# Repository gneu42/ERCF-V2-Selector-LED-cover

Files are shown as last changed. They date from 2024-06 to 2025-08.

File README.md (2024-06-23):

<h1 align="center">ERCF-Selector-LED-cover</h1> 
<H2 align="center">Under construction : use it with caution. </H2>
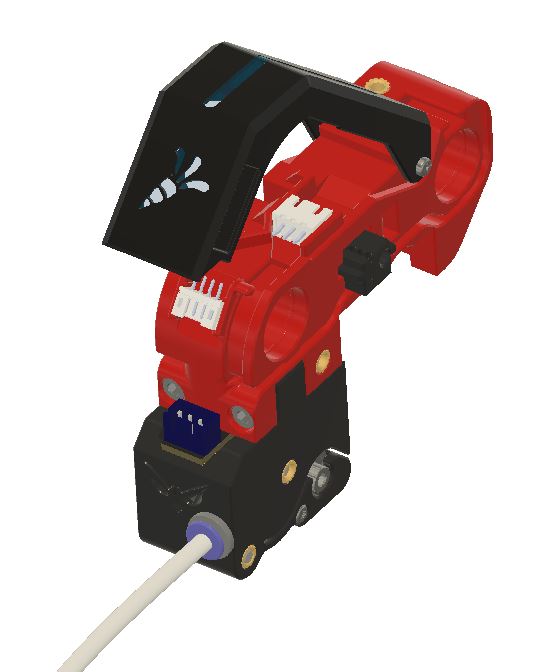
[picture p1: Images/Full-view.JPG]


**To be able to add LEDs in the selector cover, you need to print the new selector and encoder.**
* The new selector have a second cable channel on the right side to allow the LED wires to come to the front. The servo holder had its own screew now. A 4 pins PH connector power the status LED and the give the DATA to the 3 pins XH connector that feed the cover LED. 
* Why a new encoder ? Because at a certain point in time, I had a lot of problem with the encoder. I had remove it to clean it. To solve that problem I decide to move the screws to the front, and made some other improvments :
  * New adjustable berake
  * Removeble brearing cover
  * The bearing can be adjusted to be in line with the BMG
  * ECAS is hold in place tighter
  * Opening around the bearing so it can be cleaned easily.
  * The bottom secret screw is back
  * Status LED insert in the eyes. The Binky LED shows in the mouth
* The cover LED has 7 LEDs to display the filament movement, 1 LED for the leafs, and 1 LED for the carrot. 
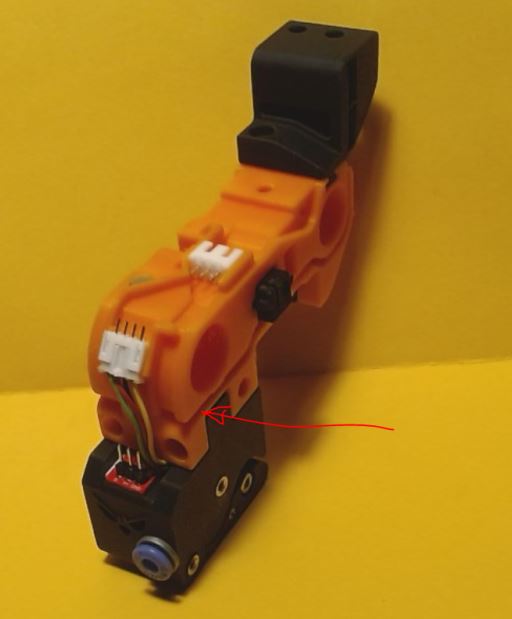
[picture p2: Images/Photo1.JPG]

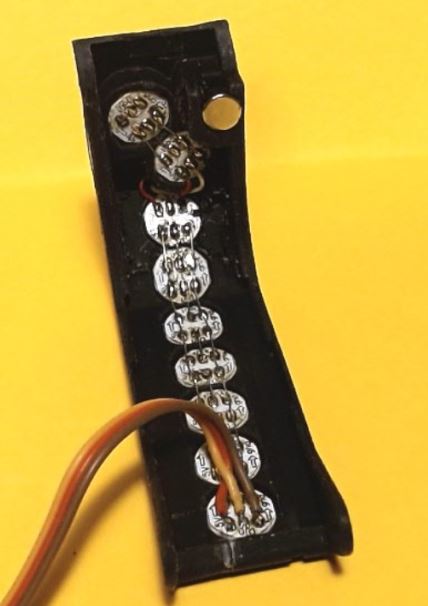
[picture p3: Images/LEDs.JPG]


The encoder and selector are tested. 
The new cover, is not yet tested.

## Summary.
* **[Bom](#bom)**
* **[Printing Tips](#printing-tips)**
* **[Assembling tips](#assembling-tips)**
 
# more to come shortly...

# BOM

# Printing tips
* The cover must be printed in 2 colors. The windows should be printed in transparent color. Load the cover in the slicer and split it into parts, then assign the colors to each bodies.

# Assembling tips

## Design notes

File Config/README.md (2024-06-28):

# **This explain how to set up the LOGO , Staus and Cover LEDs.**

##In your printer.cfg file, add :
```
   [include cover_leds_macros.cfg]
```

##In /config/mmu/base/mmu_macro_vars.cfg change the following variables 
````
[gcode_macro _MMU_STATE_VARS]
description: Happy Hare configuration for state change hooks
gcode: # Leave empty
 # You can extend functionality to all Happy Hare state change macros by
 # adding a command (or call to your gcode macro). E.g for additional
 # LED logic
 variable_user_action_changed_extension      : "_MMU_ACTION_CHANGED_COVER"    ; Executed after default logic with duplicate params
 variable_user_print_state_changed_extension : "_MMU_PRINT_STATE_CHANGED_COVER"    ; Executed after default logic with duplicate params
 variable_user_gate_map_changed_extension    : ""    ;Executed after default logic with duplicate params
 ````

**This is my personnal config as example, you must make the changes needed to match your setup :**

I have the barf led in the gearbox, 13 exit leds, no entry leds, 7 leds for the cover bar graph, 2 leds for the cover carrot logo.
    I have the following chain : 
  * From the RGB connector on the ERB board 
  * => Gearbox Barf (1-8) 
  * => Exit range (9-21) 
  * => status_index (22) 
  * => cover leds (23-29) 
  * => cover logo leafs (30) 
  * => cover logo carrot (31)

## In /config/mmu/base/mmu_hardware.cfg modify the neopixel mmu_leds according your setup.
```
[neopixel mmu_leds]
pin: mmu:MMU_NEOPIXEL
chain_count: 31              # Number gates x1 or x2 + 1 (if you want status)
color_order: GRB, GRB, GRB, GRB, GRB, GRB, GRB, GRB, GRBW, GRBW, GRBW, GRBW, GRBW, GRBW, GRBW, GRBW, GRBW, GRBW, GRBW, GRBW, GRBW, GRBW, GRBW, GRBW, GRBW, GRBW, GRBW, GRBW, GRBW, GRBW, GRBW        # Set based on your particular neopixel specification

[mmu_leds]
num_gates: 13
led_strip: neopixel:mmu_leds
exit_range: 9-21   
#entry_range: 14-{mmu_num_leds}
status_index: 22   
frame_rate: 24
```

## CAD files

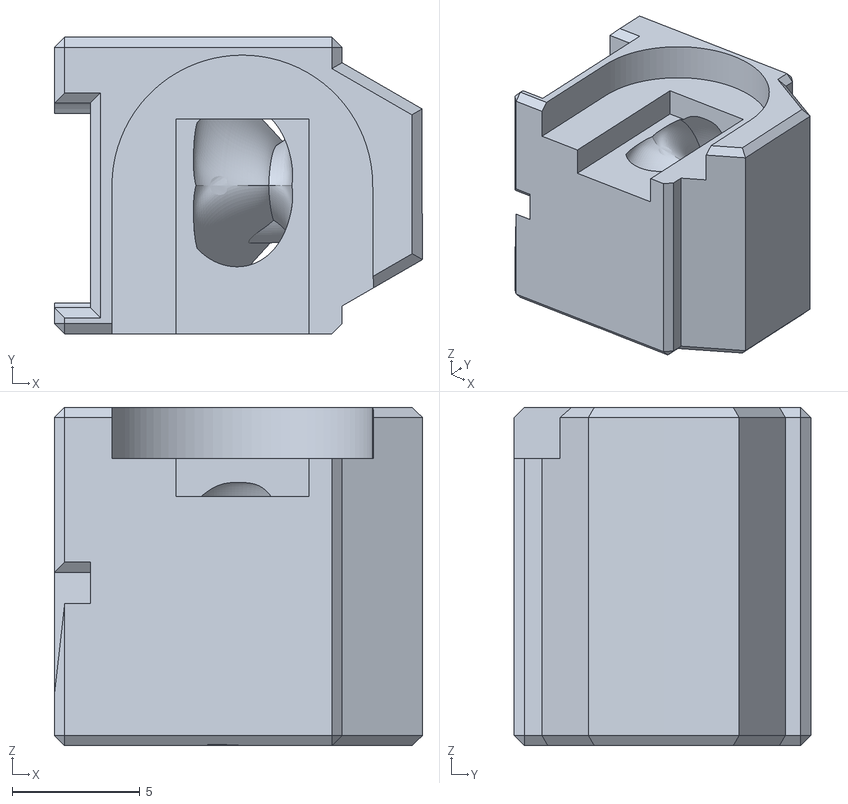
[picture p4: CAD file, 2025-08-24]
STL/[W]Encoder_Insert.stl
14.4 x 11.6 x 13.2

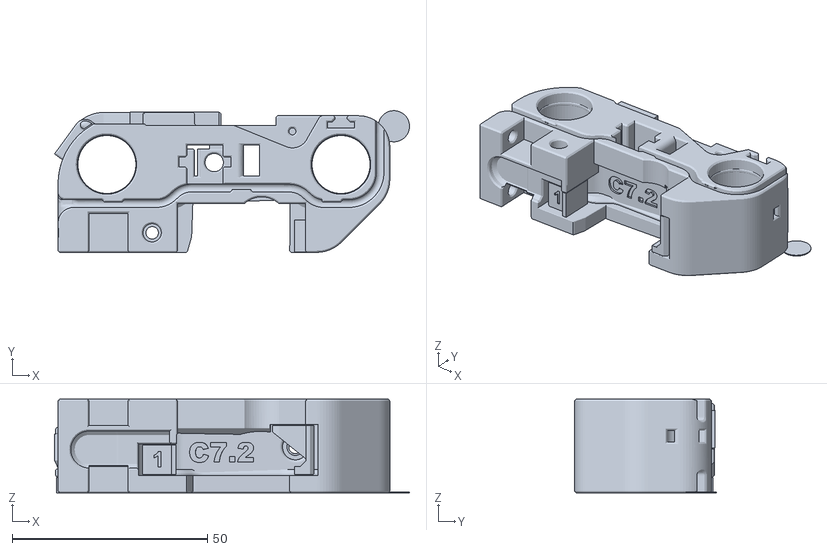
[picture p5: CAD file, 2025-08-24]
STL/[a]Selector_Cart_for_Cover_LED_Support_Corrected.stl
91.0 x 36.3 x 24.0

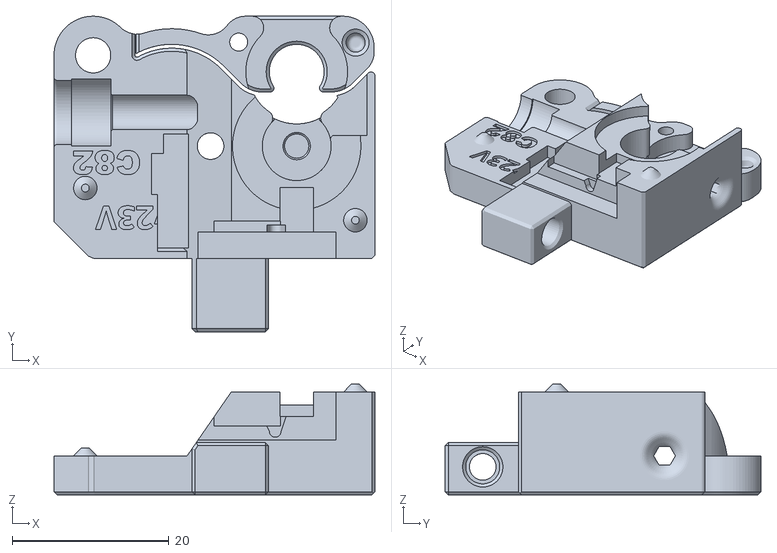
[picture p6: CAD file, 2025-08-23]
STL/Encoder_Right.stl
41.0 x 40.3 x 14.2

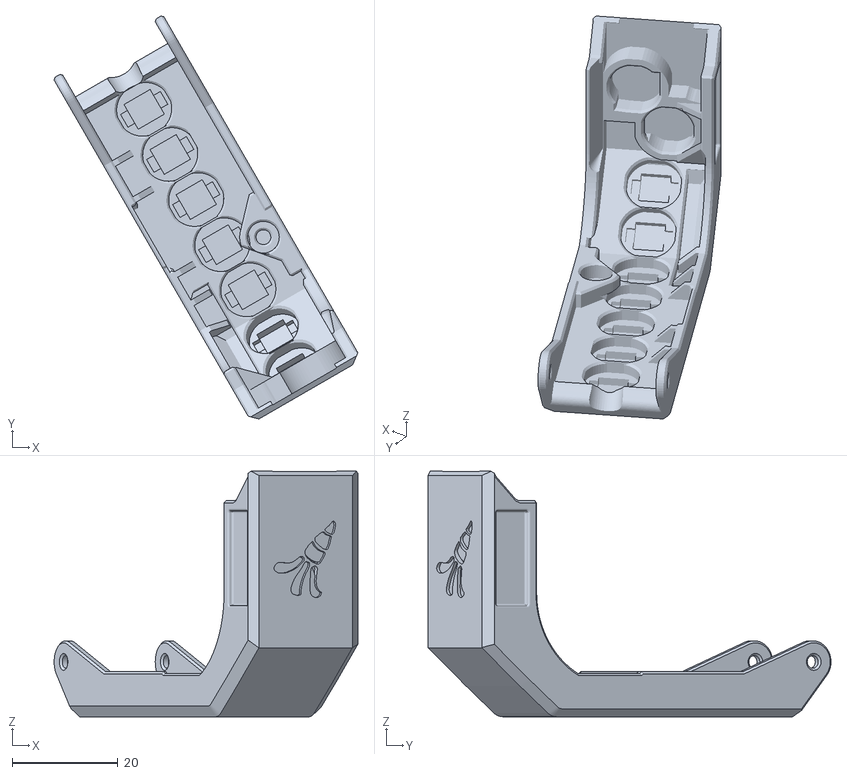
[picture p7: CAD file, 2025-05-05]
STL/Selector_Door_W_LED_Nosupports.stl
57.5 x 76.3 x 46.5

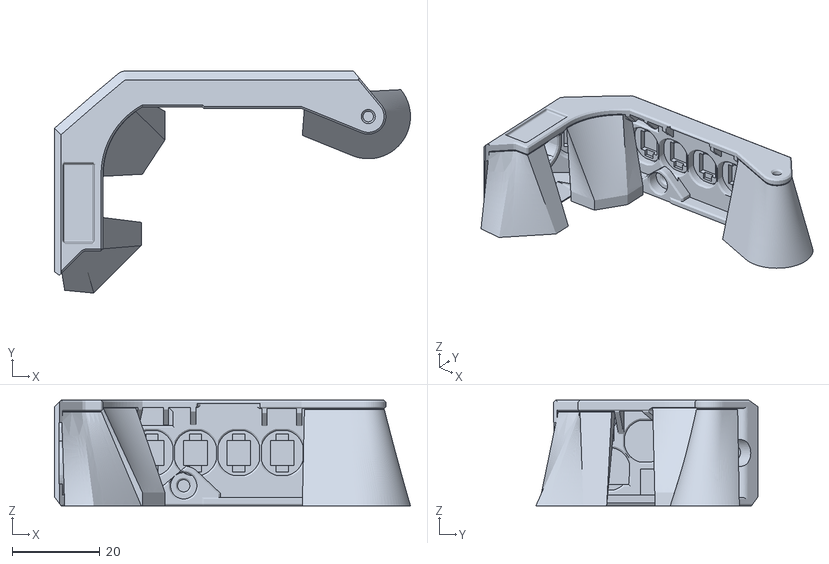
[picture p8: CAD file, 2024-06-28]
STL/Selector_Door_W_LED.stl
80.9 x 50.5 x 24.0

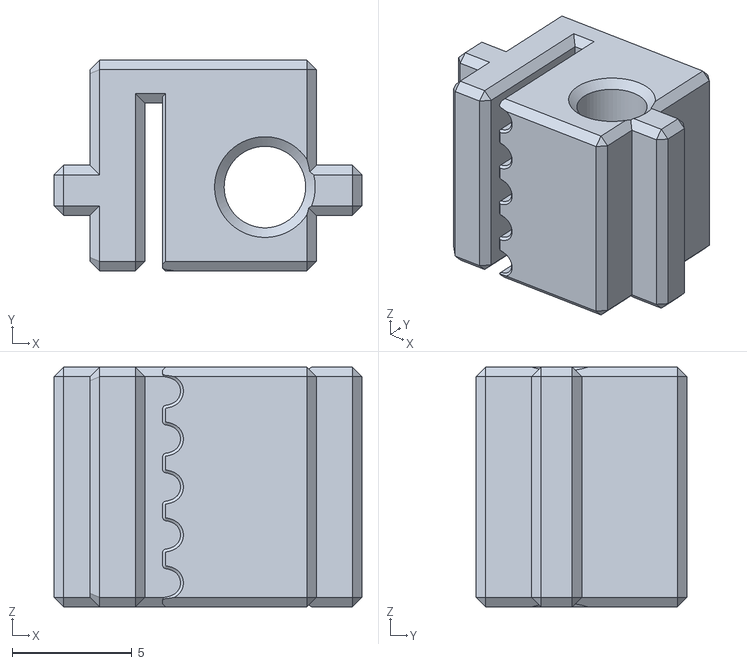
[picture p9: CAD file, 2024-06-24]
STL/Optional_Belt_Tensionner_thik.stl
12.8 x 8.80 x 10.0

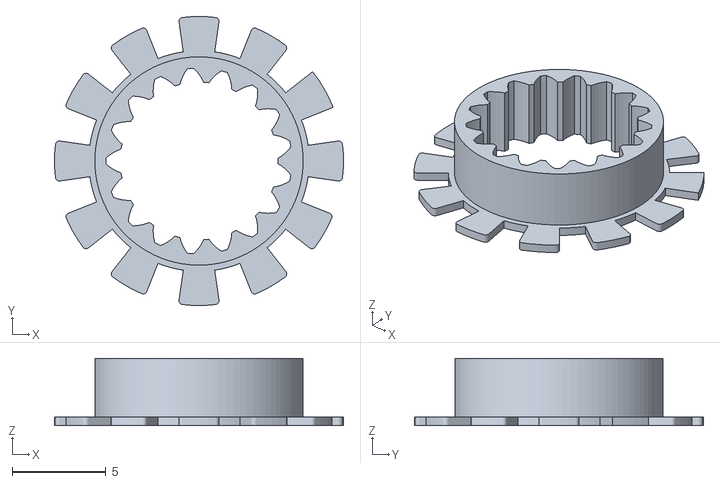
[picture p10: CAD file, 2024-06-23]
STL/[B]Optional_Slotted wheel_045mm.stl
15.4 x 15.4 x 3.58

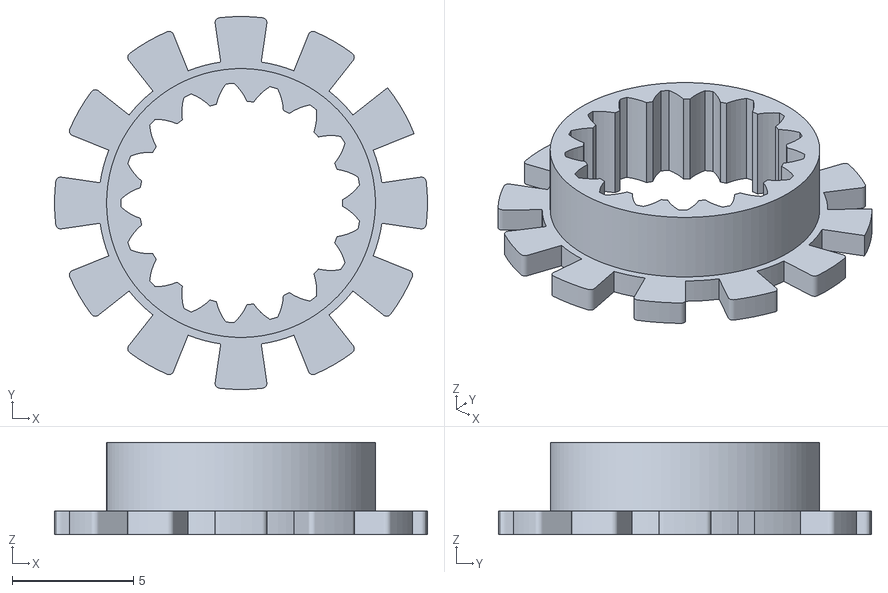
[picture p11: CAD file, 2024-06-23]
STL/[B]Original_Encoder_Slotted_Wheel.stl
15.4 x 15.4 x 3.80

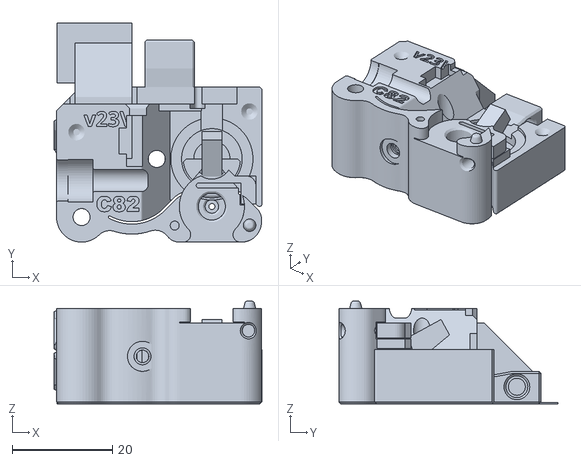
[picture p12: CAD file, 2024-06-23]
STL/Encoder_Left.stl
41.5 x 43.8 x 20.5

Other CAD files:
STL/[a]Selector_Cart_for_Cover_LED.stl

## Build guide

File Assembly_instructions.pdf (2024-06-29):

ERCF LED Cover.

Assembly manual.

This manual explain how to deal with the cover LED specific parts, please refer to the ERCF V2 manual for everything that is not in this manual.

Encoder.

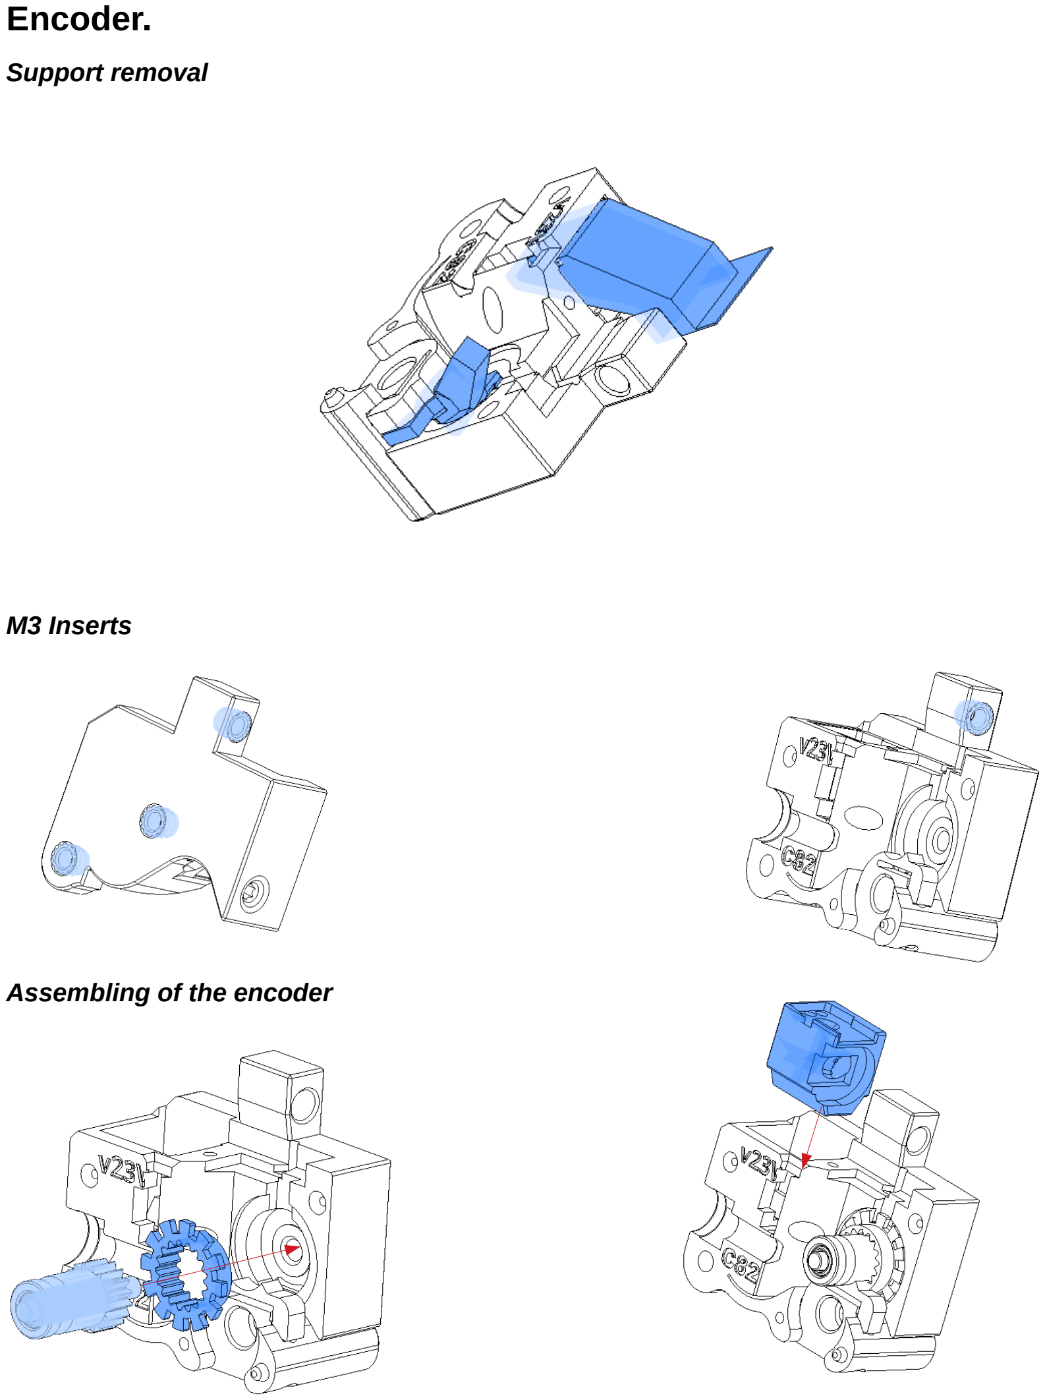
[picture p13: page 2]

Support removal

M3 Inserts

Assembling of the encoder

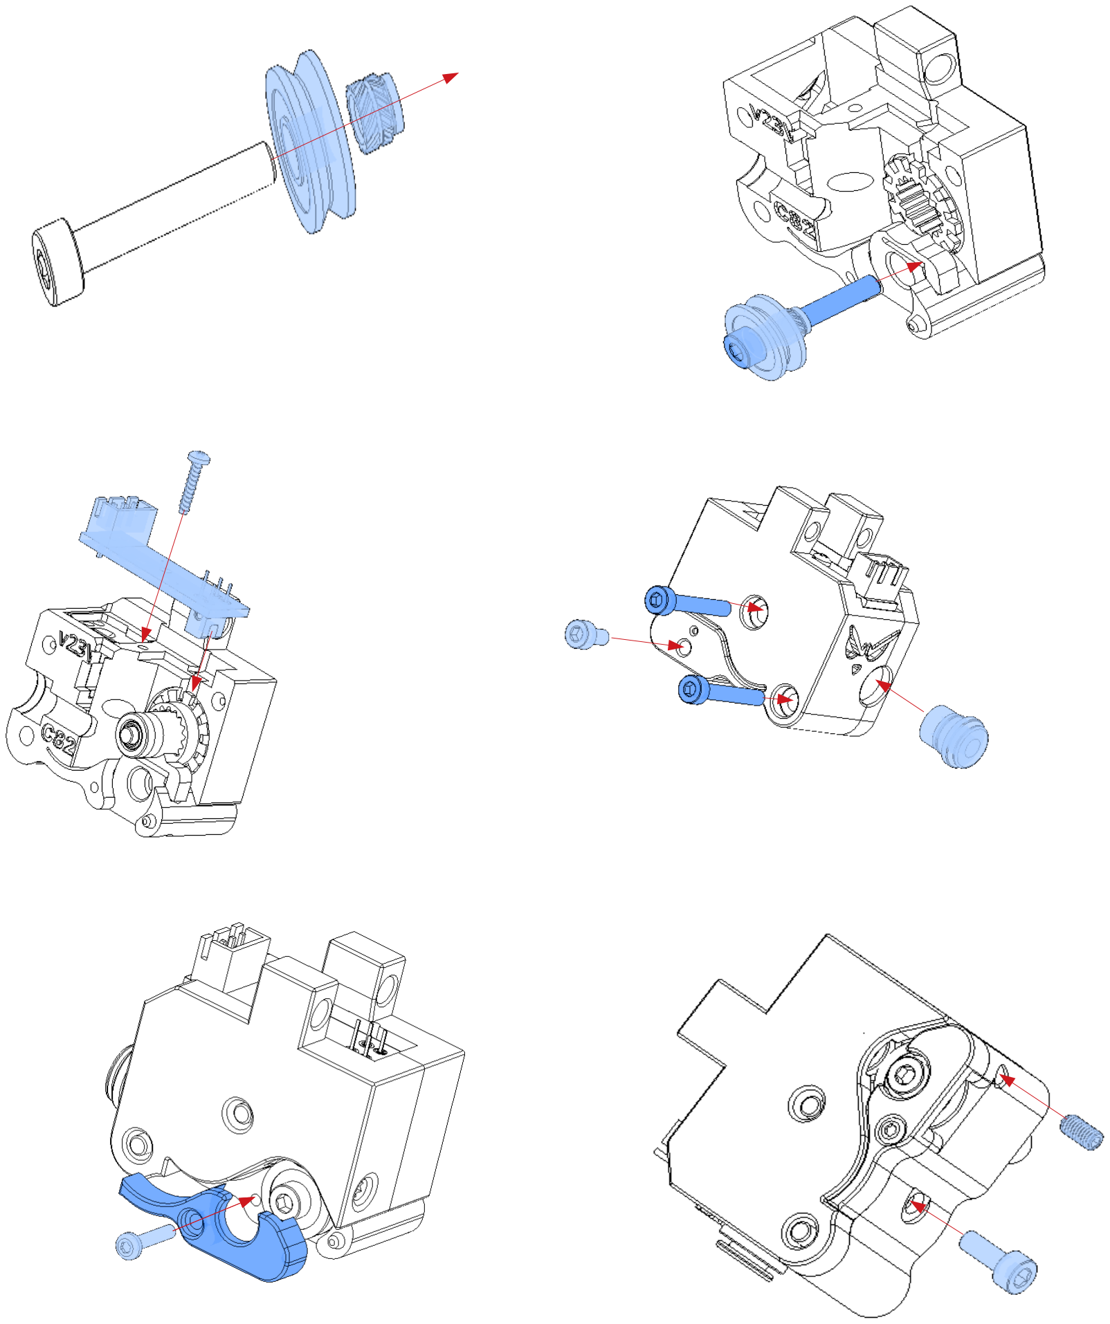
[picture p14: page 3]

## Selector

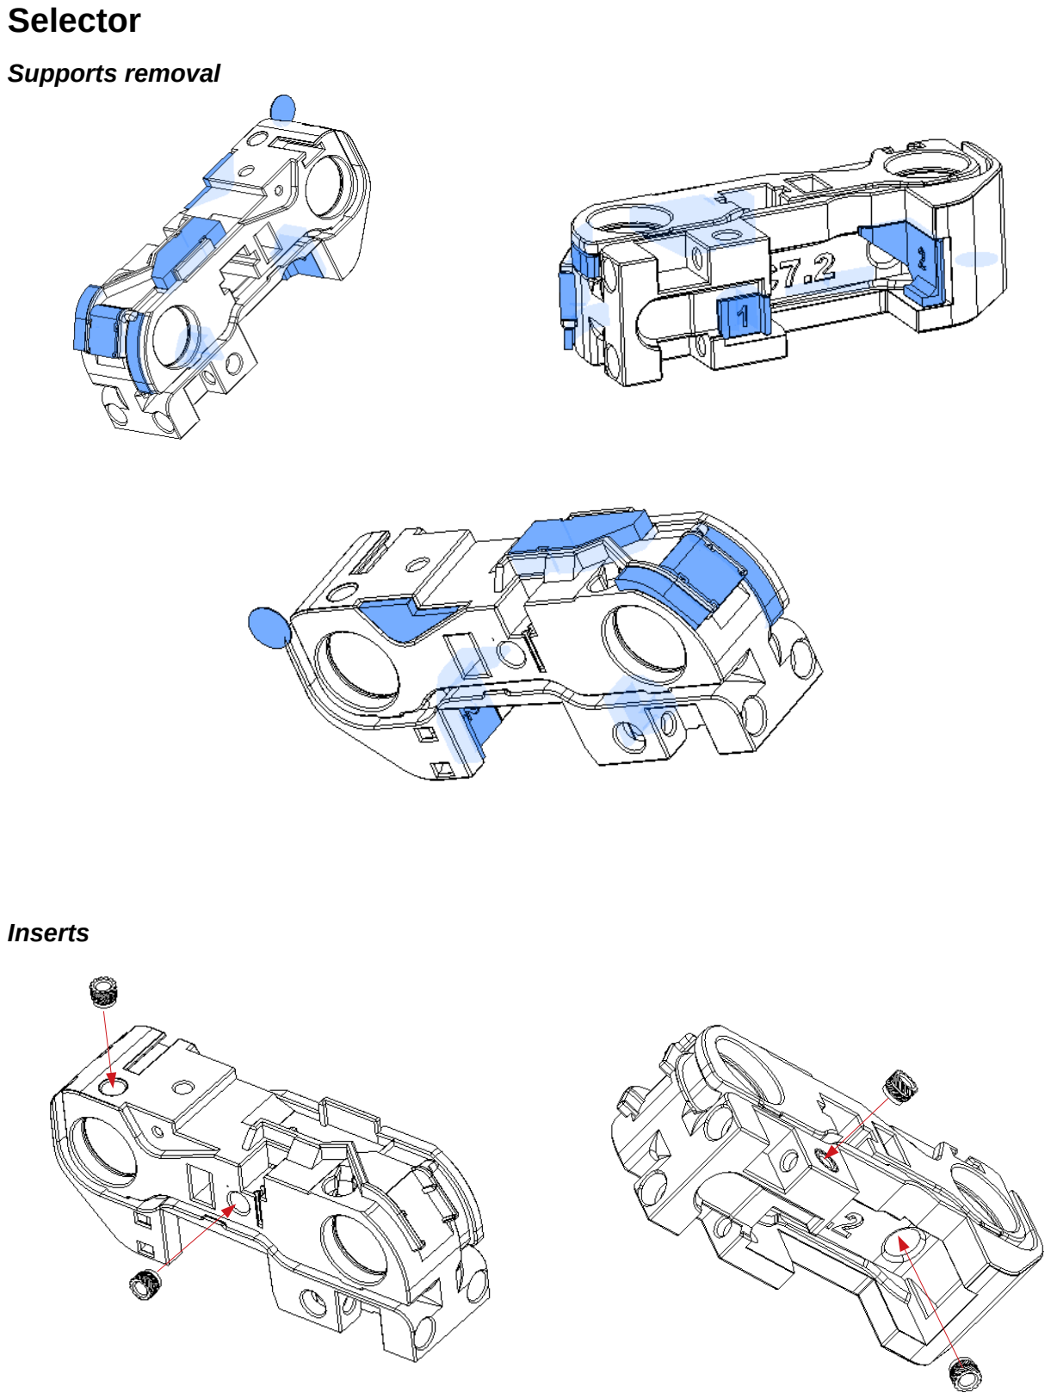
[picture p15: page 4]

Supports removal

Inserts

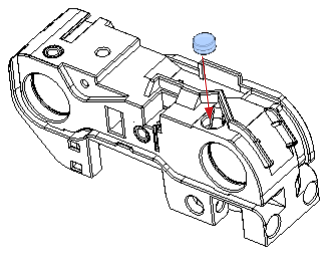
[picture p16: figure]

Magnet

Connectors

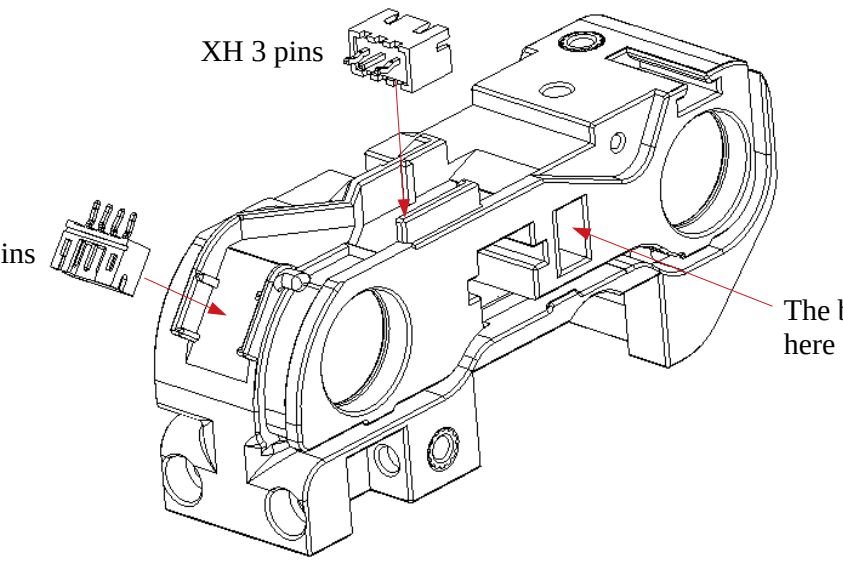
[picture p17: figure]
XH 3 pins; here

PH 4 pins
The belt pass through

## Cover Door

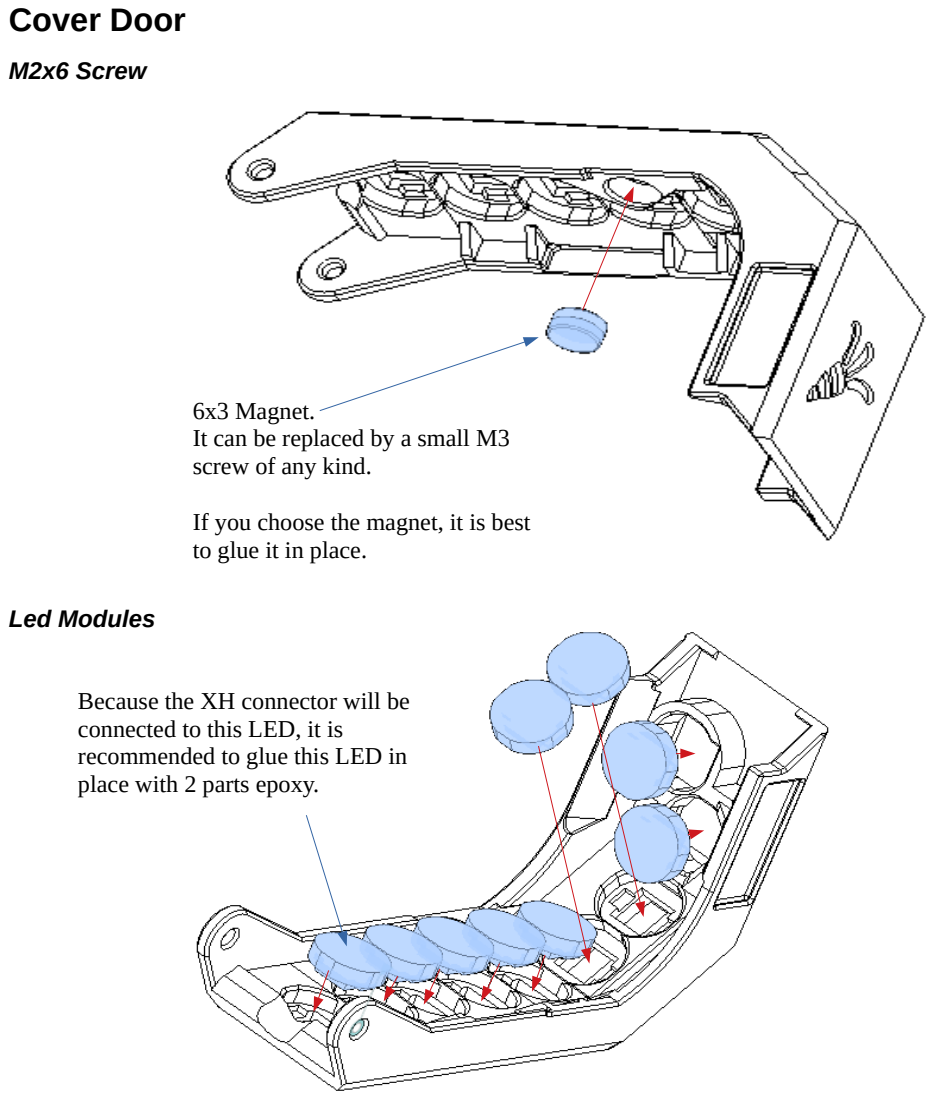
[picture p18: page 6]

M2x6 Screw

Led Modules

6x3 Magnet.
It can be replaced by a small M3 screw of any kind.

If you choose the magnet, it is best to glue it in place.

Because the XH connector will be connected to this LED, it is recommended to glue this LED in place with 2 parts epoxy.

Final assembly

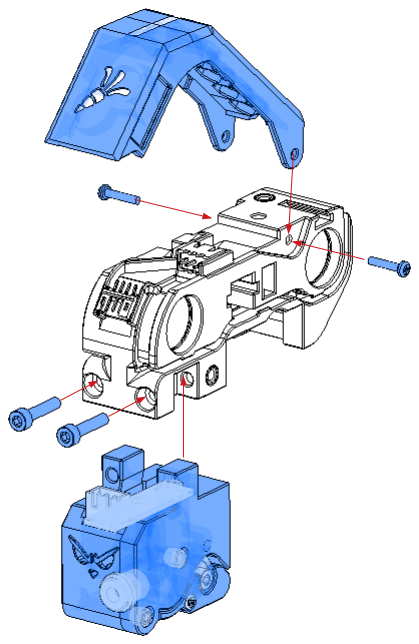
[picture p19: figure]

LED Wiring.

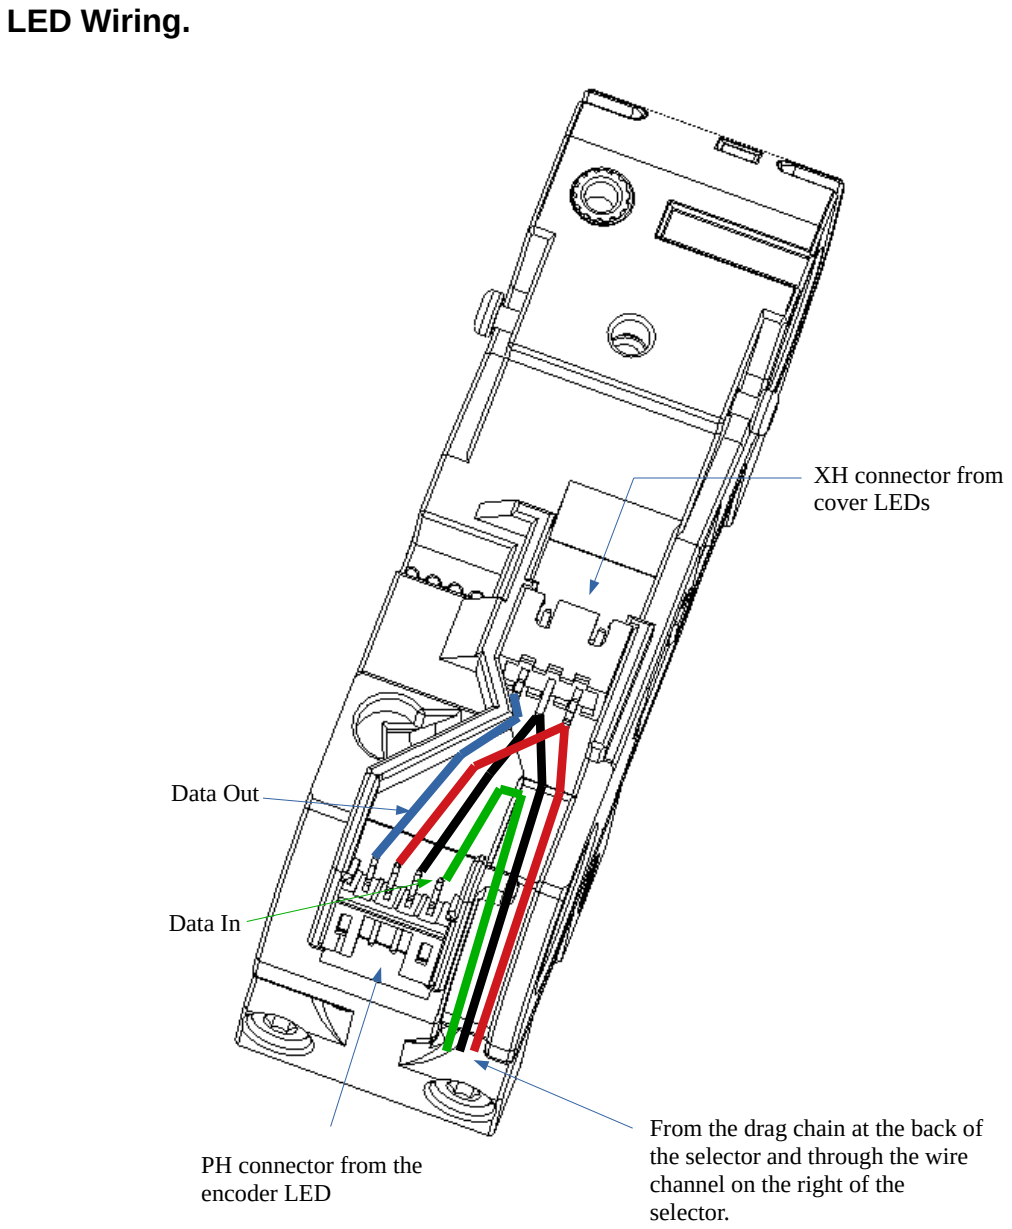
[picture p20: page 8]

Data Out

Data In

From the drag chain at the back of the selector and through the wire channel on the right of the selector.

PH connector from the
encoder LED

XH connector from
cover LEDs

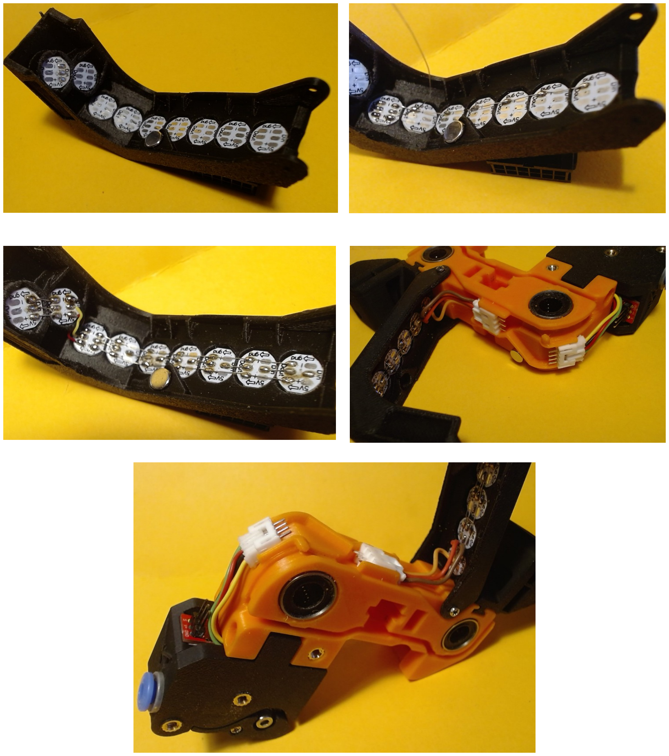
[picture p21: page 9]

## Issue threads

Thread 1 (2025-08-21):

Encoder_insert is too large & some supports for the Selector Cart Issues

o1hitman1o, 2025-08-21:
3 issues I see with this.

1) Encoder_insert is too large to fit into the Encoder_Left after print. Maybe wrong version of the file was uploaded.
2) Selector Cart has 3 supports that have a .03 mm layer separation and that is too high. They should be .02 mm like the other supports in the model.
3) Encoder_Left has a nipple on the bottom right to align the Encoder_Right "cover" that is built into the  Encoder_Right.stl but you also included Encoder_Right_Cover.stl that appears to have 2 crew holes. Is there supposed to be an addition Encoder_Left STL file that include the hole to put the screw into.

other than that I am looking forward to trying to assemble this and use it.

Closed 2025-08-24.

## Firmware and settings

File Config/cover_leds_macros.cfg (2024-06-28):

#########################################
## Cover led effect                    ##
#########################################

[include cover_leds_effects.cfg]

[gcode_macro LED_VAR]
variable_led_print_mode: 0

gcode:

################################################
# Call from _MMU_ACTION_CHANGED
################################################

[gcode_macro _MMU_ACTION_CHANGED_COVER]
description: Called by MMU_ACTION_CHANGED
gcode:
    {% set ACTION = params.ACTION|default("none")|string %}
    {% set OLD_ACTION = params.OLD_ACTION|default("none")|string %}
    {% set print_mode = printer['gcode_macro LED_VAR']['led_print_mode']|int  %}
    #M118 Action Cover = {ACTION} {OLD_ACTION}
    
    {% if ACTION == "Loading" %}
        #M118 loading
        SET_LED_EFFECT EFFECT=cover_loading REPLACE=1
        SET_LED_EFFECT EFFECT=cover_leaf REPLACE=1
        SET_LED_EFFECT EFFECT=cover_carrot REPLACE=1
        SET_LED_EFFECT EFFECT=mmu_logo_breathing45 REPLACE=1

        
    {% elif ACTION == "Loading Ext" %}
        #M118 loading ext
        #SET_LED_EFFECT EFFECT=cover_loading_done REPLACE=1
        SET_LED_EFFECT EFFECT=cover_loading_ext REPLACE=1
        SET_LED_EFFECT EFFECT=cover_leaf REPLACE=1
        SET_LED_EFFECT EFFECT=cover_carrot REPLACE=1
        SET_LED_EFFECT EFFECT=mmu_logo_breathing45 REPLACE=1
        
    {% elif ACTION == "Unloading" %}
        #M118 unloading
        SET_LED_EFFECT EFFECT=cover_unloading_ext STOP=1
        SET_LED_EFFECT EFFECT=cover_unloading REPLACE=1
        SET_LED_EFFECT EFFECT=cover_leaf REPLACE=1
        SET_LED_EFFECT EFFECT=cover_carrot REPLACE=1
        SET_LED_EFFECT EFFECT=mmu_logo_breathing45 REPLACE=1

    {% elif ACTION == "Exiting Ext" %}
        #M118 Exiting extruder
        SET_LED_EFFECT EFFECT=cover_unloading STOP=1
        SET_LED_EFFECT EFFECT=cover_unloading_ext REPLACE=1
        SET_LED_EFFECT EFFECT=cover_leaf REPLACE=1
        SET_LED_EFFECT EFFECT=cover_carrot REPLACE=1
        SET_LED_EFFECT EFFECT=mmu_logo_breathing45 REPLACE=1
        
    {% elif ACTION == "Heating" %}
        #M118 Heating
        SET_LED_EFFECT EFFECT=cover_heating REPLACE=1
        SET_LED_EFFECT EFFECT=cover_leaf REPLACE=1
        SET_LED_EFFECT EFFECT=cover_carrot REPLACE=1
        SET_LED_EFFECT EFFECT=mmu_logo_heating REPLACE=1
        
    {% elif ACTION == "Idle" %}
        {% if print_mode == 1 %}
        #  M118 idle after and print mode
           SET_LED_EFFECT EFFECT=cover_printing REPLACE=1
           SET_LED_EFFECT EFFECT=cover_leaf_static REPLACE=1
           SET_LED_EFFECT EFFECT=cover_carrot_static REPLACE=1
           SET_LED_EFFECT EFFECT=mmu_logo_printing REPLACE=1
        
        {% else  %}       #OLD_ACTION == "Loading"
        #  M118 idle after loading
           SET_LED_EFFECT EFFECT=cover_idle REPLACE=1
           SET_LED_EFFECT EFFECT=cover_leaf_static REPLACE=1
           SET_LED_EFFECT EFFECT=cover_carrot_static REPLACE=1
           SET_LED_EFFECT EFFECT=mmu_logo_printing REPLACE=1
        {% endif %}
    
     {% elif ACTION == "Selecting" and OLD_ACTION == "Checking" %}
        #M118 checking
        SET_LED_EFFECT EFFECT=cover_checking REPLACE=1
        SET_LED_EFFECT EFFECT=cover_leaf REPLACE=1
        SET_LED_EFFECT EFFECT=cover_carrot REPLACE=1
        SET_LED_EFFECT EFFECT=mmu_logo_breathing REPLACE=1
        
    {% elif ACTION == "Homing" or ACTION == "Selecting" %}
        #M118 Homing or selecting
        SET_LED_EFFECT EFFECT=cover_homing REPLACE=1
        SET_LED_EFFECT EFFECT=cover_leaf REPLACE=1
        SET_LED_EFFECT EFFECT=cover_carrot REPLACE=1
        SET_LED_EFFECT EFFECT=mmu_logo_breathing45 REPLACE=1
    
    {% elif ACTION == "Checking" %}
        SET_LED_EFFECT EFFECT=cover_checking REPLACE=1
        SET_LED_EFFECT EFFECT=cover_leaf REPLACE=1
        SET_LED_EFFECT EFFECT=cover_carrot REPLACE=1
        SET_LED_EFFECT EFFECT=mmu_logo_breathing REPLACE=1
        
    {% elif ACTION == "none" %}
        #M118 None
        SET_LED_EFFECT EFFECT=cover_action_missing REPLACE=1
        SET_LED_EFFECT EFFECT=mmu_logo REPLACE=1
    
    
    
    {% endif %}


###########################################################################
# This occurs when the MMU print state changes. The `STATE` parameter will contain
# the current state string (also available in `printer.mmu.print_state` printer variable)
# Also the previous action is available in `OLD_STATE`. See Happy Hare README for
# full list of state strings and the state transition diagram.
#
# Quick State Ref:
#  initialized|ready|started|printing|complete|cancelled|error|pause_locked|paused|standby
#
# The reference logic here drives a set of optional LED's
#
[gcode_macro _MMU_PRINT_STATE_CHANGED_COVER]
description: Called by MMU_PRINT_STATE_CHANGED

gcode:
    
    {% set STATE = params.STATE|default("none")|string %}
    {% set OLD_STATE = params.OLD_STATE|default("none")|string %}
    # M118 State = {STATE} {OLD_STATE}
    {% if STATE == "initialized" %} 
       #M118 STATE = Initialize
       SET_LED_EFFECT EFFECT=cover_curtain REPLACE=1
       SET_LED_EFFECT EFFECT=mmu_logo_init REPLACE=1
       _MMU_RESET_COVER
    {% elif STATE == "printing" %}
        #M118 STATE = printing
        SET_GCODE_VARIABLE MACRO=LED_VAR VARIABLE=led_print_mode VALUE=1
        SET_LED_EFFECT EFFECT=cover_printing REPLACE=1
        SET_LED_EFFECT EFFECT=cover_leaf_static REPLACE=1
        SET_LED_EFFECT EFFECT=cover_carrot_static REPLACE=1
        SET_LED_EFFECT EFFECT=mmu_logo_printing REPLACE=1
    {% elif STATE == "pause_locked" %}
        SET_LED_EFFECT EFFECT=cover_strobe REPLACE=1
        SET_LED_EFFECT EFFECT=mmu_logo REPLACE=1
    {% elif STATE == "paused" %}
       SET_LED_EFFECT EFFECT=cover_strobe REPLACE=1
       SET_LED_EFFECT EFFECT=mmu_logo REPLACE=1
    {% elif STATE == "ready" %}
        SET_LED_EFFECT EFFECT=cover_breathing_orange REPLACE=1
        SET_LED_EFFECT EFFECT=mmu_logo REPLACE=1
    {% elif STATE == "complete" %}
        SET_GCODE_VARIABLE MACRO=LED_VAR VARIABLE=led_print_mode VALUE=0
        SET_LED_EFFECT EFFECT=cover_idle REPLACE=1
        SET_LED_EFFECT EFFECT=cover_leaf REPLACE=1
        SET_LED_EFFECT EFFECT=cover_carrot REPLACE=1
        SET_LED_EFFECT EFFECT=mmu_logo REPLACE=1
    {% elif STATE == "error" %}
        SET_LED_EFFECT EFFECT=cover_strobe REPLACE=1
        SET_LED_EFFECT EFFECT=mmu_logo REPLACE=1
    {% elif STATE == "cancelled" %}
        SET_GCODE_VARIABLE MACRO=LED_VAR VARIABLE=led_print_mode VALUE=0
        SET_LED_EFFECT EFFECT=cover_idle REPLACE=1
        SET_LED_EFFECT EFFECT=cover_leaf_static REPLACE=1
        SET_LED_EFFECT EFFECT=cover_carrot_static REPLACE=1
        SET_LED_EFFECT EFFECT=mmu_logo REPLACE=1
    {% elif STATE == "standby" %}
        #SET_LED_EFFECT EFFECT=cover_breathing_orange REPLACE=1
        SET_LED_EFFECT EFFECT=mmu_standby REPLACE=1
        SET_LED_EFFECT EFFECT=cover_leaf_strobe REPLACE=1
        SET_LED_EFFECT EFFECT=cover_carrot_strobe REPLACE=1
        SET_LED_EFFECT EFFECT=mmu_logo_standby REPLACE=1
    {% elif STATE == "none" %}
        SET_LED_EFFECT EFFECT=cover_state_missing REPLACE=1
        SET_LED_EFFECT EFFECT=mmu_logo REPLACE=1
        
    {% endif %}



#############################################
## Reset to default
#############################################
[gcode_macro _MMU_RESET_COVER]
description: Called by _MMU_RESET_LED

gcode:
    SET_LED_EFFECT EFFECT=cover_idle REPLACE=1
    SET_LED_EFFECT EFFECT=cover_leaf_static REPLACE=1
    SET_LED_EFFECT EFFECT=cover_carrot_static REPLACE=1
    SET_LED_EFFECT EFFECT=mmu_logo_breathing REPLACE=1

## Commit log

2024-06-23 Rename STL
    [Encoder Left insert.stl, Encoder Left.stl, Encoder Right.stl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]
2024-06-24 Add Assembly instrucions
    [Encoder_Left.stl, Encoder_Right.stl, Encoder_Right_Cover.stl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]
2024-06-28 Update Selector door with 6x3 magnet.
    [Selector_Door_W_LED.stl]
2024-06-28 add config files and update readme
    [cover_leds_effects.cfg, cover_leds_macros.cfg]
2025-08-23 Update some STL
    [Encoder_Right.stl, Encoder_Right_Cover.stl, [W]Encoder_Insert.stl]
2025-08-24 Update selector and insert STLs
    [[W]Encoder_Insert.stl, [a]Selector_Cart_for_Cover_LED_Support_Corrected.stl]
